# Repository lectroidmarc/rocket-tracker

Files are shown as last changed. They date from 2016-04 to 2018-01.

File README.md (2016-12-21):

# Rocket Tracker

This is the code for a [model rocket](https://en.wikipedia.org/wiki/Model_rocket) tracking system, to find (lost) model rockets via GPS.

The idea is that a GPS transmitter will live in a rocket and transmit data to a ground station via radio.  That ground station will then update a "cloud" based data store with the location(s) of the rocket(s).  A user (or users) can then access that data with any internet connected device (phone, tablet, laptop etc) to see the locations of their rockets.

Easy.

This system can be used by individuals for tracking one or more rockets or by large groups for tracking larger numbers of rockets.

The system is made up of the following components:

* ##### The GPS Transmitter

  The GPS transmitter is a small microcontroller that connects to a GPS and some kind of [XBee radio](http://www.digi.com/lp/xbee).  The micorcontroller parses the NMEA data from the GPS and transmits location data once per second over the radio.

  Transmission packets are 9 byte packets made up of a status byte then 4 bytes for latitude and 4 bytes for longitude (each are 4 byte floats).

* ##### The Ground Station

  The ground station listens for location messages from the transmitters and then forwards their location to a [Firebase](https://firebase.google.com) based database.

  If ZigBee radios are used, the ground station is also the network coordinator.

  The ground station code itself is a simple [NodeJS](https://nodejs.org/) app and so can run on anything that can run NodeJS and has a serial port to talk to an XBee radio.  And has internet access.

* ##### The Client App

  The client app is what the user uses to see the location of their rocket.  It connects to Firebase and displays the location data in (near) real time and allows the user to open the rocket's location in a mapping app.  Client web app code is located in the [gh-pages branch](../../tree/gh-pages) and can be seen at https://lectroidmarc.github.io/rocket-tracker/.

* ##### Dumb Relays (optional)

  If using ZigBee radios, every GPS transmitter is already a "router" but dedicated routers could also be added to extend range or enhance coverage.  These are simple ZigBee routers node that have no other logic to them, just powered pre-configured radios.

#### XBee Radio Setup

Generally speaking the only thing that needs to be changed from a factory default XBee radio is that they need to be placed into [API Mode 2](http://knowledge.digi.com/articles/Knowledge_Base_Article/What-is-API-Application-Programming-Interface-Mode-and-how-does-it-work).  Everything else can be handled in software.

For [ZigBee](https://en.wikipedia.org/wiki/ZigBee) radios, the proper ZigBee firmware (Coordinator, Router or End Device) will have to be installed.  For our purposes there's no advantage to the "End Device" firmware, so it's just one Coordinator and multiple Routers.

Note: Alternatively, settings (such as the PAN ID) can be pre-configured in each module.  In these cases, comment out the matching settings in the configuration file so they're not overwritten.

##### Dumb Relay nodes

Dumb relay nodes however should be configured in firmware with the PAN ID (`ATID`) and with Channel Verification turned on (`ATJV1`).

#### To Do

* The XBee protocols support status packets so the transmitter can use the lack of a successful status packet as a signal to enable some alternate means of discovery -- like enabling a loud buzzer after a certain timeout.

* Include some sort of built-in internet connectivity in the ground station.

* Expose the location data via a custom Bluetooth LE GATT profile on the ground station and allow the clients in range to use the [Web Bluetooth API](https://webbluetoothcg.github.io/web-bluetooth/) to fetch and display the data.  Note, with Bluetooth, _only one client can connect at a time_.

-30-

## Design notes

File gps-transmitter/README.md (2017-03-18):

# GPS Transmitter

There are currently two GPS Transmitter prototypes, a [Sparkfun Fio v3](https://learn.sparkfun.com/tutorials/pro-micro--fio-v3-hookup-guide) or an [Adafruit Feather M0](https://www.adafruit.com/products/2772).  Each are set up to use an [Adafruit Ultimate GPS](https://learn.adafruit.com/adafruit-ultimate-gps).

It can handle different types of "Pro" series XBee radios including: [Series 1](https://www.sparkfun.com/products/11216), [900mhz XBee-PRO](https://www.sparkfun.com/products/11634) or [Zigbee modules (S2B or S2C)](https://www.adafruit.com/products/967).  Zigbee moduels are preferred as they offer mesh capabilities.  The radio is always on `Serial1`.

The M0 is the preferred platform as it can report battery level as well as provides backup power to the GPS.

### Configuration

Configuration is handled in `config.h`.  Uncomment the block that matches the XBee radio type you have.  There are different blocks for each supported XBee radio type so only uncomment one set at a time.

For the Fio v3, set the GPS pins you wish to use (remember on the Fio, only certain pins can be used for recieving under SoftwareSerial). On the M0 pins 10 and 12 are mapped to `Serial2`, and the GPS is hardcoded to use that.

-30-

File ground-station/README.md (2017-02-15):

# Ground Station

This is a [NodeJS](https://nodejs.org) app to handle incoming location data from an XBee radio and output it to [Firebase](https://firebase.google.com).  This assumes a working network connection of course ;).

### Configuration

Rename the `config.sample.js` file to `config.js` and edit what needs to be edited.  Basically this means setting the name of your Firebase DB and what setting the serial port your XBee radio is attached to.

There are different blocks for each supported XBee radio type, XBee Series 1, XBee-PRO 900 and XBee Zigbee modules.  Many options are duplicated for so only uncomment one set at a time.

#### Firebase Service Account

To talk to Firebase, the node app assumes you have a valid [Service Account key file](https://firebase.google.com/docs/server/setup#prerequisites) saved to `serviceAccountKey.json`.

### Manual Starting

Start the listener with:

    # node node/app

### Auto Starting (systemd)

If using systemd, install the `ground-station.service.txt` file into `/etc/systemd/system/ground-station.service`.  Then enable it with the following:

    # systemctl enable ground-station
    # systemctl start ground-station

Of course the opposite is:

    # systemctl stop ground-station
    # systemctl disable ground-station

Status checks can be done with:

    # systemctl status ground-station

And log checks with:

    # journalctl -u ground-station

### Network Reset

When using ZigBee radios the channel is automatically chosen by the Coordinator when the PAN is first configured.  If for some reason you need to move to a different channel, you can force a rescan of the available channels by triggering a network reset (`ATNR1`) with the following command:

    # node network-reset

This will also send a network reset broadcast to all associated nodes causing them to update as well.

_Very Important: Any nodes that are not actively associated (i.e. those currently lost) will not get the message to reset their network settings so they will lose connectivity._

-30-

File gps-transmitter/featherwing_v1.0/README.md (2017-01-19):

# GPS Transmitter M0 FeatherWing v1.0

These are [Eagle](http://www.autodesk.com/products/eagle/overview) files for a "FeatherWing", basically a sheild, for an [Adafruit Feather M0 Basic Proto](https://www.adafruit.com/products/2772) that supports both a XBee radio and an [Adafruit Ultimate GPS v3](https://www.adafruit.com/products/746).

Additionally the M0 BAT pin is tied to the GPS VBAT pin to enable hot start functionality.

Besides the Feather M0, Ultimate GPS and the appropriate XBee module, the following BOM is needed for a fully functioning FeatherWing

* 1x - [Short Feather Male Headers](https://www.adafruit.com/products/3002)
* 1x - [2mm 10 pin XBee Socket Headers](https://www.adafruit.com/products/366)
* 1x - [Standard 0.1" female headers](https://www.adafruit.com/products/598)
* 1x - [2-pin, 3.5mm pitch, screw terminal](https://www.adafruit.com/products/724)
* 2x56 (or M2) screws for mounting

-30-

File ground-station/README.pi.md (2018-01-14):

# Raspberry Pi Setup

Install and setup [Raspbian Lite](https://www.raspberrypi.org/downloads/raspbian/).

Install NodeJS _(assumes Node 8.9.4 on a Pi A, B, B+ or Zero (armv6))_:

    wget https://nodejs.org/dist/v8.9.4/node-v8.9.4-linux-armv6l.tar.xz
    sudo tar -xf node-v8.9.4-linux-armv6l.tar.xz -C /usr/local --strip-components=1

Install git:

    sudo apt-get install git

Clone this repo.

    git clone https://github.com/lectroidmarc/rocket-tracker.git

Build the node modules (this will take a very long time on a slow Pi):

    cd rocket-tracker/ground-station/node
    npm install

(Optional) Install the systemd system file

    cd ..
    sudo cp ground-station.service.txt /etc/systemd/system/ground-station.service

-30-

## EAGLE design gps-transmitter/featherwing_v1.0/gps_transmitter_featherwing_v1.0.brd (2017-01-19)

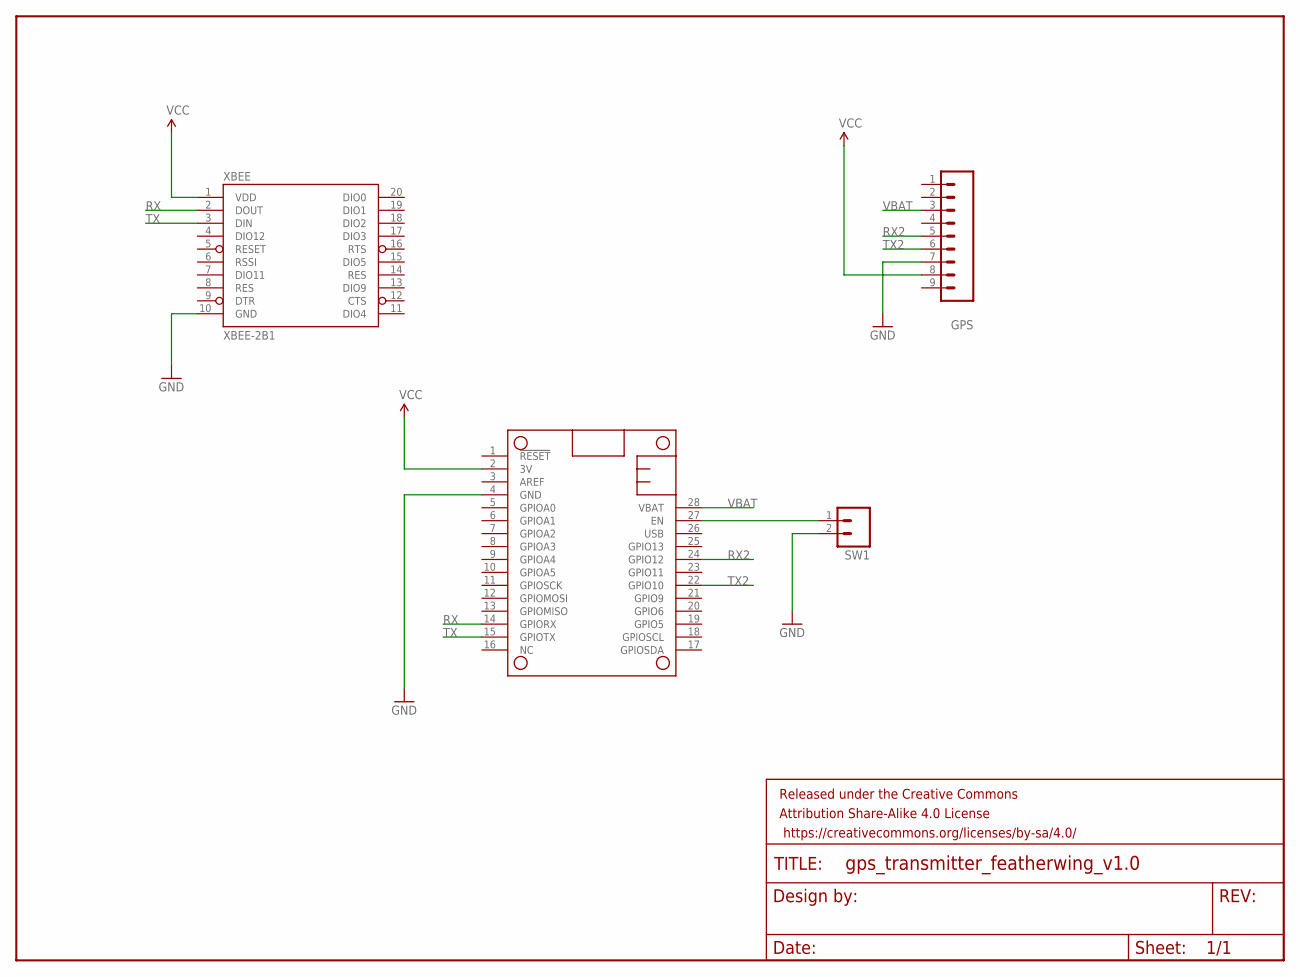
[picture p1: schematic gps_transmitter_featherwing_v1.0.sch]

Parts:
FRAME1: FRAME-LETTER; CREATIVE_COMMONS
GPS: M09; 1X09
MS1: FEATHERWING_NODIM; FEATHERWING_DIM
SW1: M023.5MM; SCREWTERMINAL-3.5MM-2
XBEE: XBEE-2B1; XBEE-1

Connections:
GND: GPS.7, MS1.4 (GND), SW1.2, XBEE.10 (GND)
unnamed: MS1.27 (EN), SW1.1
RX: MS1.14 (GPIORX), XBEE.2 (DOUT)
RX2: GPS.5, MS1.24 (GPIO12)
TX: MS1.15 (GPIOTX), XBEE.3 (DIN)
TX2: GPS.6, MS1.22 (GPIO10)
VBAT: GPS.3, MS1.28 (VBAT)
VCC: GPS.8, MS1.2 (3V), XBEE.1 (VDD)

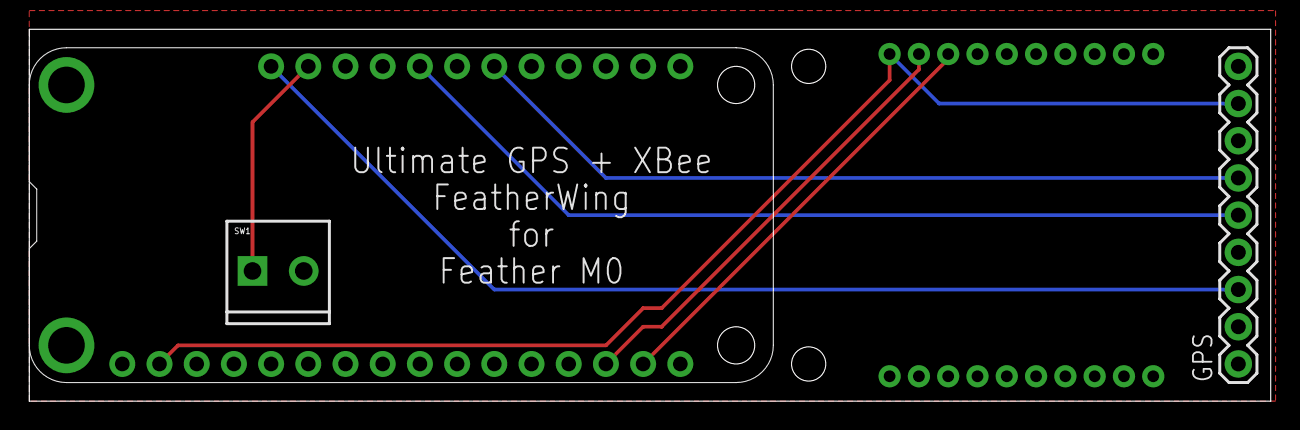
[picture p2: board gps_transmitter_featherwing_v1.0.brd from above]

Board: 2 copper layers, 84.8 x 25.4 mm, 5 parts (1 on the bottom side), 8 nets.

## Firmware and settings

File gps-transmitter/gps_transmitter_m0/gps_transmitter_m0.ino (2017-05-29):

/*
 * GPS Transmitter
 *
 * Utilizes a Adafruit Feather M0. Creates Serial2 on pins 10 (TX) and 12 (RX)
 * and uses it for the GPS.  An XBee radio is on Serial1.
 */

#include <Arduino.h>        // required before wiring_private.h
#include "wiring_private.h" // pinPeripheral() function

#include <Adafruit_GPS.h>
#include <XBee.h>

#include "config.h"
#include "xbee_helpers.h"

// Set up Serial2 on pins 10 (TX) and 12 (RX)
// See: https://learn.adafruit.com/using-atsamd21-sercom-to-add-more-spi-i2c-serial-ports/creating-a-new-serial
Uart Serial2(&sercom1, 12, 10, SERCOM_RX_PAD_3, UART_TX_PAD_2);

XBee xbee = XBee();

byte payload[9];
byte gps_status = 0x00;

XBeeAddress64 ground_station = XBeeAddress64(GROUND_STATION_ADDR_HI, GROUND_STATION_ADDR_LO);

#ifdef XBEE_ZB
  ZBTxRequest zbTx = ZBTxRequest(ground_station, payload, sizeof(payload));
  ZBTxStatusResponse zbTxStatus = ZBTxStatusResponse();
#else
  Tx64Request tx = Tx64Request(ground_station, payload, sizeof(payload));
  TxStatusResponse txStatus = TxStatusResponse();
#endif

Adafruit_GPS GPS(&Serial2);

// Interrupt handler for SERCOM1
void SERCOM1_Handler() {
  GPS.read();
  //char c = GPS.read();
  //if (c) Serial.print(c);
  Serial2.IrqHandler();
}

void setup() {
  //Serial.begin(9600);

  Serial1.begin(9600);
  xbee.setSerial(Serial1);

#ifdef XBEE_PAN_ID
  setXBeePanId(XBEE_PAN_ID);
#endif

#ifdef XBEE_CHANNEL
  setXBeeMyAddress(0xffff);     // Set to force 64 bit addressing
  setXBeeChannel(XBEE_CHANNEL);
#endif

#ifdef XBEE_HOPPING_CHANNEL
  setXBeeHoppingChannel(XBEE_HOPPING_CHANNEL);
#endif

#ifdef XBEE_VERIFY_CHANNEL
  setXBeeChannelVerification(XBEE_VERIFY_CHANNEL);
#endif

  // GPS.begin() doesn't quite work with the SERCOM stuff...
  Serial2.begin(9600);

  pinPeripheral(10, PIO_SERCOM);
  pinPeripheral(12, PIO_SERCOM);

  GPS.sendCommand(PMTK_SET_NMEA_OUTPUT_RMCONLY);
  GPS.sendCommand(PMTK_SET_NMEA_UPDATE_1HZ);
//  GPS.sendCommand("$PMTK220,2000*1C");  // NMEA update every 2 seconds
//  GPS.sendCommand("$PMTK220,5000*1B");  // NMEA update every 5 seconds

  pinMode(13, OUTPUT);  // Use the onboard LED as an error light for XBee packet failures
}

void loop() {
  if (GPS.newNMEAreceived()) {
    if (!GPS.parse(GPS.lastNMEA())) {
      return;
    }

    //Serial.print(GPS.lastNMEA());

    // status bit 0 is fix status
    if (GPS.fix) {
      gps_status |= 1 << 0;
    } else {
      gps_status &= ~(1 << 0);
    }

    // status bit 1 says we have battery info
    gps_status |= 1 << 1; // bit 1 says we have battery info

    // status bits 2 - 4 are battery info
    float measuredvbat = analogRead(A7);
    measuredvbat *= 2;    // we divided by 2, so multiply back
    measuredvbat *= 3.3;  // Multiply by 3.3V, our reference voltage
    measuredvbat /= 1024; // convert to voltage

    gps_status &= ~(7 << 2);  // clear bits 2 - 4

    /*
     * Battery status based on the following:
     *
     * 4.14 volts or more is "full".
     * 3.60 volts is the lowest usable voltage.
     *
     * So 4.14 volts works out to 95% so it shows as "full" while
     * 3.60 volts works out to just above 15% which is the cutoff
     * for "!".  Everything else just falls in the middle.
     */
    float batteryPercentage = (10 - (4.17 - measuredvbat) / 0.0672) * 10;
    if (batteryPercentage > 95) {
      gps_status |= 7 << 2;   // 100%
    } else if (batteryPercentage > 85) {
      gps_status |= 6 << 2;   // 90%
    } else if (batteryPercentage > 75) {
      gps_status |= 5 << 2;   // 80%
    } else if (batteryPercentage > 65) {
      gps_status |= 5 << 2;   // 70% but stay at 80%
    } else if (batteryPercentage > 55) {
      gps_status |= 4 << 2;   // 60%
    } else if (batteryPercentage > 45) {
      gps_status |= 3 << 2;   // 50%
    } else if (batteryPercentage > 35) {
      gps_status |= 3 << 2;   // 40% but stay at 50%
    } else if (batteryPercentage > 25) {
      gps_status |= 2 << 2;   // 30%
    } else if (batteryPercentage > 15) {
      gps_status |= 1 << 2;   // 20%
    }

    setPayload(gps_status, GPS.latitudeDegrees, GPS.longitudeDegrees, payload);

#ifdef XBEE_ZB
    xbee.send(zbTx);
#else
    xbee.send(tx);
#endif

    if (xbee.readPacket(1000)) {
#ifdef XBEE_ZB
      if (xbee.getResponse().getApiId() == ZB_TX_STATUS_RESPONSE) {
        xbee.getResponse().getZBTxStatusResponse(zbTxStatus);
        uint8_t deliveryStatus = zbTxStatus.getDeliveryStatus();
#else
      if (xbee.getResponse().getApiId() == TX_STATUS_RESPONSE) {
        xbee.getResponse().getTxStatusResponse(txStatus);
        uint8_t deliveryStatus = txStatus.getStatus();
#endif
        if (deliveryStatus == SUCCESS) {
          digitalWrite(13, LOW);
        } else {
          digitalWrite(13, HIGH);

          //Serial.print("Delivery Error: 0x");
          //Serial.println(deliveryStatus, HEX);
        }
      }
    }
  }
}

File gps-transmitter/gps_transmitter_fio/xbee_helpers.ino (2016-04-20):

/*
 *
 */

uint8_t setXBeePanId (uint16_t addr) {
  uint8_t cmd[] = {  'I', 'D' };
  uint8_t value[2];

  value[0] = (addr >> 8) & 0xff;
  value[1] = addr & 0xff;

  AtCommandRequest atRequest = AtCommandRequest(cmd, value, sizeof(value));
  xbee.send(atRequest);
  return getAtResponse();
}

uint8_t setXBeePanId (uint64_t addr) {
  uint8_t cmd[] = {  'I', 'D' };
  uint8_t value[8];

  value[0] = (addr >> 56) & 0xff;
  value[1] = (addr >> 48) & 0xff;
  value[2] = (addr >> 40) & 0xff;
  value[3] = (addr >> 32) & 0xff;
  value[4] = (addr >> 24) & 0xff;
  value[5] = (addr >> 16) & 0xff;
  value[6] = (addr >> 8) & 0xff;
  value[7] = addr & 0xff;

  AtCommandRequest atRequest = AtCommandRequest(cmd, value, sizeof(value));
  xbee.send(atRequest);
  return getAtResponse();
}

uint8_t setXBeeMyAddress (uint16_t addr) {
  uint8_t cmd[] = {  'M', 'Y' };
  uint8_t value[2];

  value[0] = (addr >> 8) & 0xff;
  value[1] = addr & 0xff;

  AtCommandRequest atRequest = AtCommandRequest(cmd, value, sizeof(value));
  xbee.send(atRequest);
  return getAtResponse();
}

uint8_t setXBeeChannel (uint8_t channel) {
  uint8_t cmd[] = {  'C', 'H' };
  uint8_t value[] = { channel };

  AtCommandRequest atRequest = AtCommandRequest(cmd, value, sizeof(value));
  xbee.send(atRequest);
  return getAtResponse();
}

uint8_t setXBeeHoppingChannel (uint8_t channel) {
  uint8_t cmd[] = {  'H', 'P' };
  uint8_t value[] = { channel };

  AtCommandRequest atRequest = AtCommandRequest(cmd, value, sizeof(value));
  xbee.send(atRequest);
  return getAtResponse();
}

uint8_t setXBeeChannelVerification (uint8_t mode) {
  uint8_t cmd[] = {  'J', 'V' };
  uint8_t value[] = { mode };

  AtCommandRequest atRequest = AtCommandRequest(cmd, value, sizeof(value));
  xbee.send(atRequest);
  return getAtResponse();
}

uint8_t setXBeeNetworkWatchdogTimeout (uint16_t timeout) {
  uint8_t cmd[] = {  'N', 'W' };
  uint8_t value[2];

  value[0] = (timeout >> 8) & 0xff;
  value[1] = timeout & 0xff;

  AtCommandRequest atRequest = AtCommandRequest(cmd, value, sizeof(value));
  xbee.send(atRequest);
  return getAtResponse();
}

uint8_t resetXBeeNetwork (uint8_t mode) {
  uint8_t cmd[] = {  'N', 'R' };
  uint8_t value[] = { mode };

  AtCommandRequest atRequest = AtCommandRequest(cmd, value, sizeof(value));
  xbee.send(atRequest);
  return getAtResponse();
}

uint8_t getAtResponse () {
  AtCommandResponse atResponse = AtCommandResponse();

  if (xbee.readPacket(1000)) {
    if (xbee.getResponse().getApiId() == AT_COMMAND_RESPONSE) {
      xbee.getResponse().getAtCommandResponse(atResponse);
      if (atResponse.isOk()) {
        return 0;
      } else {
        return atResponse.getStatus();
      }
    }
  }
}

void setPayload (byte status, float lat, float lng, uint8_t* payload) {
  binaryFloat latitude;
  binaryFloat longitude;

  latitude.floatingPoint = lat;
  longitude.floatingPoint = lng;

  payload[0] = status;

  payload[1] = latitude.binary[0];
  payload[2] = latitude.binary[1];
  payload[3] = latitude.binary[2];
  payload[4] = latitude.binary[3];

  payload[5] = longitude.binary[0];
  payload[6] = longitude.binary[1];
  payload[7] = longitude.binary[2];
  payload[8] = longitude.binary[3];
}

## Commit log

2016-04-18 Support battery status.
    Use the next 3 bits after status to hold 8 battery modes.
2016-04-20 Add the 64 bit PAN ID bug fix.
    [xbee_helpers.ino]
2016-04-22 Add some serial port error checking.
    [app.js]
2016-12-21 Confused by the LED macros...
2017-01-07 Improve battery reporting.
2017-01-07 Match the error lighting with the M0.
    [gps_transmitter_fio.ino, gps_transmitter_m0.ino]
2017-01-07 Remove NMEA verifcation code.
    This was fixed in Adafruit GPS Library version 1.0.1.
    [gps_transmitter_fio.ino, gps_transmitter_m0.ino]
2017-01-07 Sync up error reporting between the Fio and M0.
    [gps_transmitter_fio.ino, gps_transmitter_m0.ino]
2017-01-19 Add Eagle design files for the first board.
    [gps_transmitter_featherwing_v1.0.brd, gps_transmitter_featherwing_v1.0.sch]
2017-03-12 Improved battery reporting.
2017-03-12 Actually stay at 50% battery :/
2022-06-02 Bump protobufjs from 6.10.2 to 6.11.3 in /ground-station/node
    Bumps [protobufjs](https://github.com/protobufjs/protobuf.js) from 6.10.2 to 6.11.3.
    - [Release notes](https://github.com/protobufjs/protobuf.js/releases)
    - [Changelog](https://github.com/protobufjs/protobuf.js/blob/v6.11.3/CHANGELOG.md)
    - [Commits](https://github.com/protobufjs/protobuf.js/compare/v6.10.2...v6.11.3)
    ---
    updated-dependencies:
    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

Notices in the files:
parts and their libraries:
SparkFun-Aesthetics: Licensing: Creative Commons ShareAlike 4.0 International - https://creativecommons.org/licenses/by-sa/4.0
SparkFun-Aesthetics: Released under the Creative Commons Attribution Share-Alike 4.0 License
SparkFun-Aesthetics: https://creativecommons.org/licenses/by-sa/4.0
